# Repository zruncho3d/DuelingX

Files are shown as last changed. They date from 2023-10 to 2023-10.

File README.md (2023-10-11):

# Dueling X

**Dueling X (DX) is a flexible Fusion 360 CAD file to enable your own Dual Gantry (DG) 3D printer.**

**Dual Gantry** printers are _badass dual-head speed demons_.  

They have all the benefits of two toolheads, without the speed disadvantages inherent in IDEX printers, or the complexity and risk inherent in toolchangers.   [Here's one (Dueling Zero v3)](https://github.com/zruncho3d/DuelingZero):

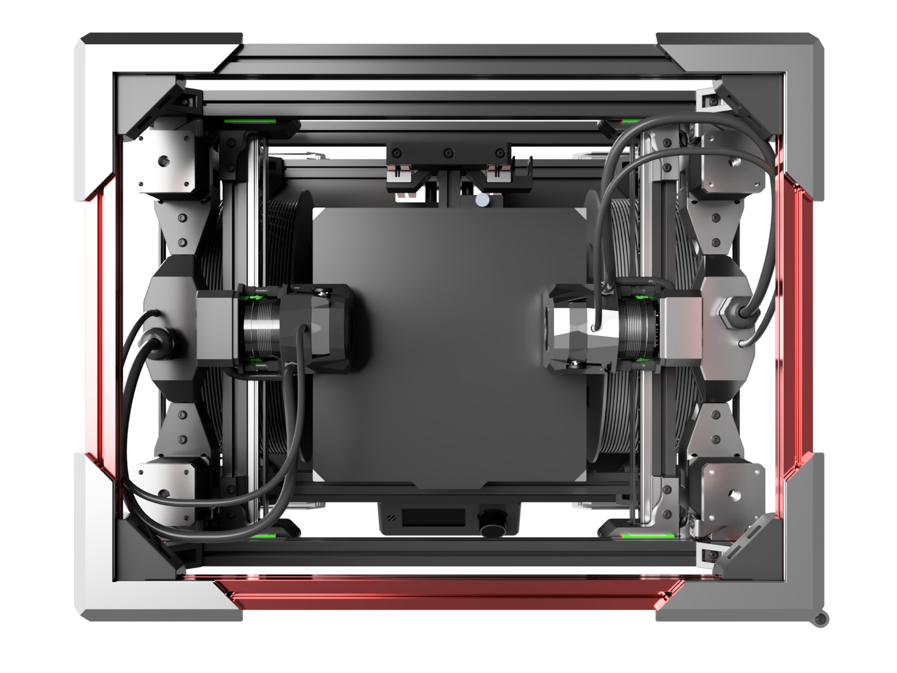
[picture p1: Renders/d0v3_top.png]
text


Not your average printer, right?  In short, the mechanical side of DG is reasonably mature, but the configuration and calibration side is still developing... so, consider it scary-but-exciting territory, for the adventurous.

**Dueling X** is a parametric gantry design based on the original Dueling Zero v3 symmetric gantry, built to enable larger and more varied DG printers.  Use the larger extrusions, rails, motors, from a Voron Trident kit, or customize the build for whatever you have on hand.

This is *not* a complete printer generator, yet.  Think of it as a printed-part generator for a gantry, with stock sizes ready to go, but which still enables customizations.  From above, the printed parts and belts paths look like this, to scale:

| Type 0 (V0 parts): Medium | Type 1 (Trident parts): Large | Type 2 (Trident Maximus parts): XL | Your own parts! |
| - | - | - | - |
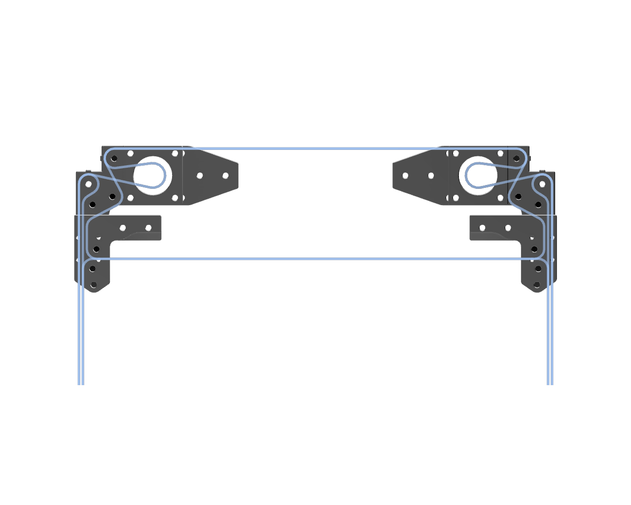
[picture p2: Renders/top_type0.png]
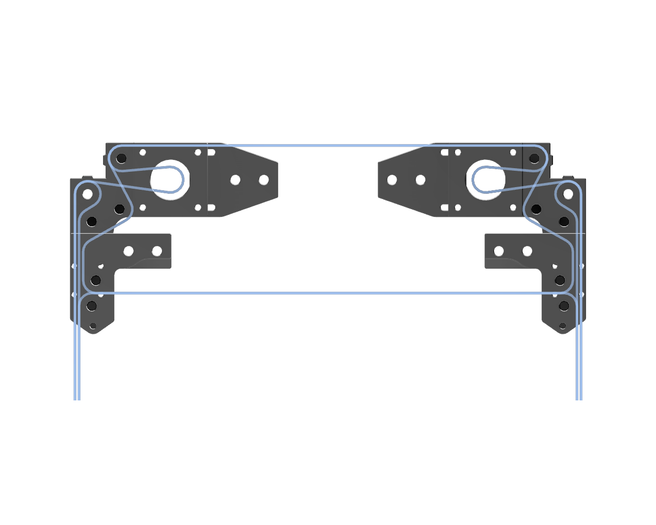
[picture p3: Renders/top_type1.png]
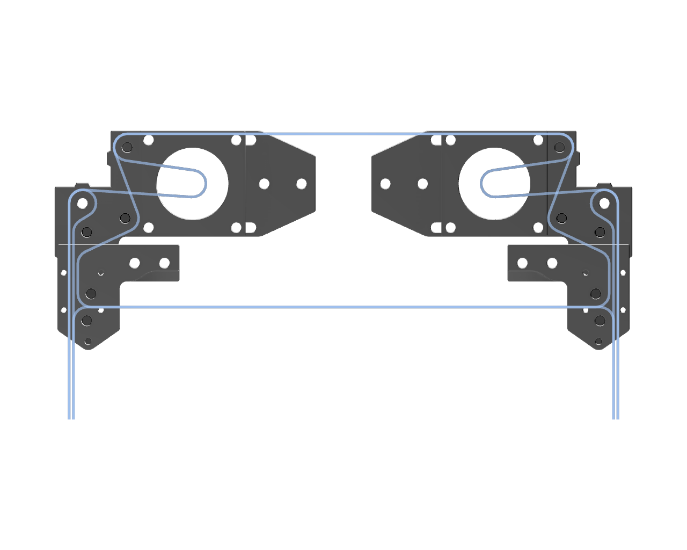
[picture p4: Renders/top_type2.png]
|  |  |  | **?...** |
| 1515/NEMA14/F623/6mm/MGN7+9 | 2020/NEMA17/F695/6mm/MGN9+12 | 3030+2020/F695/9mm/MGN12 | **?...** |

Similar shapes, yet completely different "parts bins" and sizes!

| Sample iso view | 3 stock sizes on one plate |
| - | - |
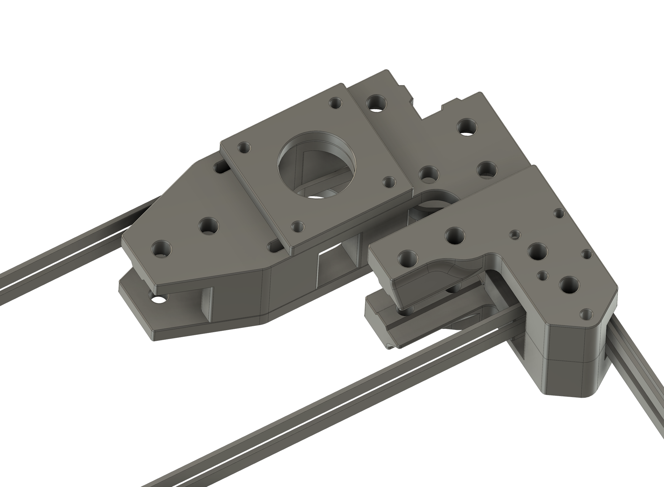
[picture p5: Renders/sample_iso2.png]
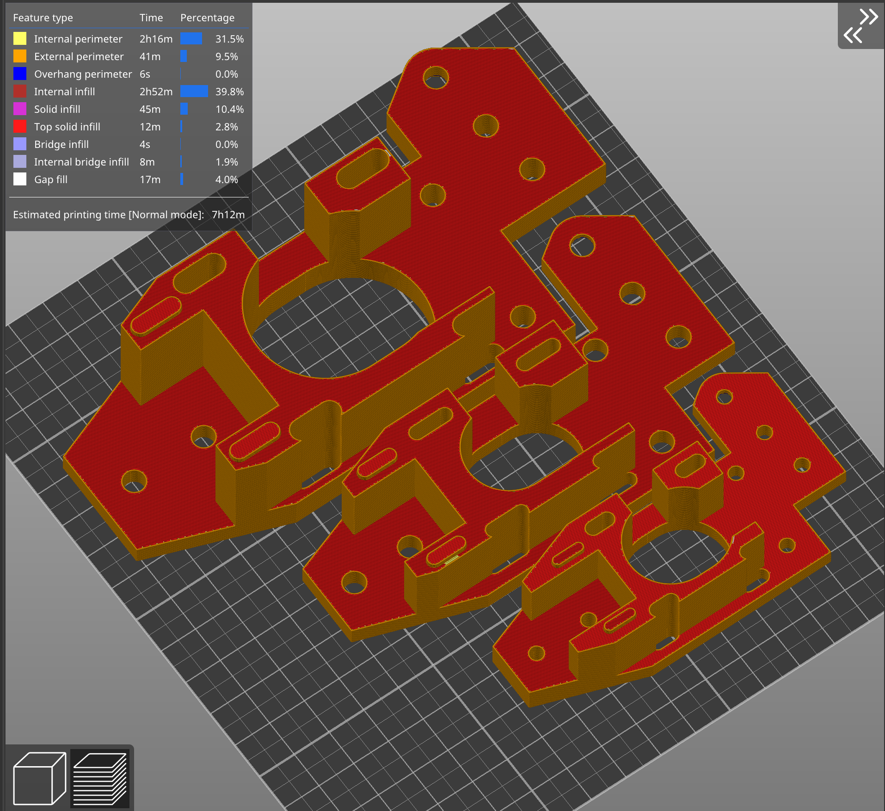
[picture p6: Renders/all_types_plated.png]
|  |  |

The STLs above were generated by changing the `type` value between the 3 values, waiting a few seconds for the model to recompute, and exporting an STL after each change.

Main features of DX:
* **3 main stock sizes (medium, large, XL)**, where each uses a different parts kit (Voron Zero, Voron Trident, Trident Maximus), but can still be customized to your preferred parts.  See the Standard Configurations table below.
* **Pandora-derived gantry**, for the win.  Top-mount outer rails, with bearings above, yields high XY density (build area relative to frame area).  
* **Front-facing toolhead rail** enables:
  * compatibility with many carriages, including small ones (Micron, Boop,...) and large ones (Clockwork, Archetype Core, ...)  
  * compatibility with many toolheads, including small ones (Dragon Burner, MiniSB, ...) and large ones (Stealthburner, Xol, Archteype, ...)
* **Symmetric design**: like the Dueling Zero v3 gantry from which it derives, Dueling X is symmetric, which heavily reduces the custom-plastic-parts count and complexity.  The P shape of the belts in a CoreXY printer are carefully nested in the XY plane, which has all kinds of benefits relative to prior approaches, at only the cost of about 10mm travel.

What makes this model possible?  Heavy use of parameters and equations in the Fusion 360 CAD.  See [this walkthrough video](https://www.youtube.com/watch?v=n0W37SkbVsI) for an explanation of how conditional parameters and naming conventions work in this file.  In the future, as Fusion 360 Configurations become available, managing the configurations may become even easier!

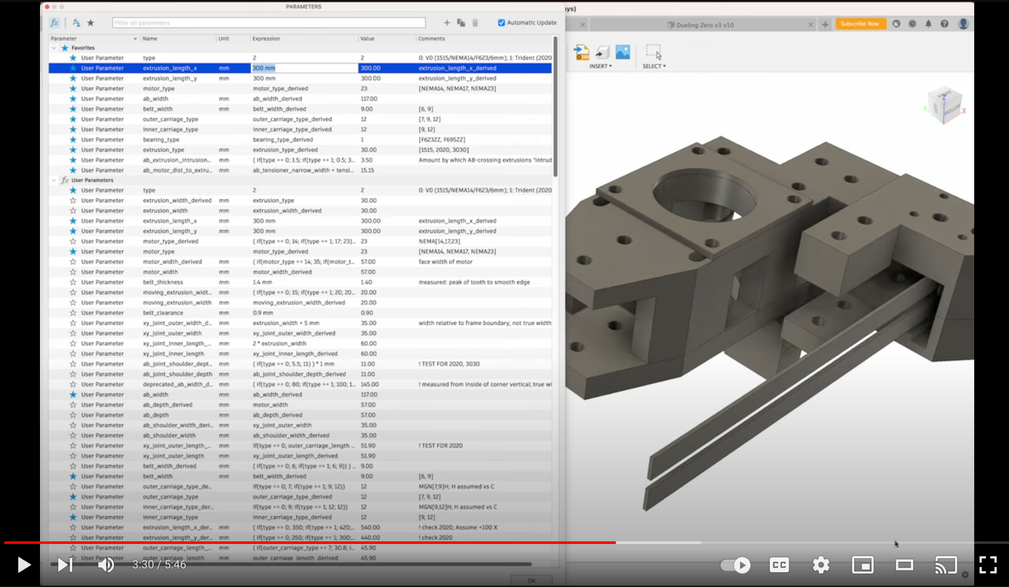
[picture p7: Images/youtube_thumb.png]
(https://www.youtube.com/watch?v=n0W37SkbVsI)


Take a look around... DG printers are weird and wonderful, yet suprisingly practical, and I'm hoping to see more builds, now that the 2020 options are available.

Like what you see?  [Buy me a coffee](https://ko-fi.com/zruncho3d) to show the love and enable future mods and content, stuff like [F0](https://github.com/zruncho3d/f-zero), [T0](https://github.com/zruncho3d/tri-zero), [B0](https://github.com/zruncho3d/boxzero), [X0](https://github.com/zruncho3d/double-dragon), [D0](https://github.com/zruncho3d/DuelingZero), [ZeroPanels](https://github.com/zruncho3d/ZeroPanels), [NoDropNuts](https://github.com/zruncho3d/f-zero/tree/main/STLs/NoDropNuts), [Boop](https://github.com/PrintersForAnts/Boop) improvements, and more.

:heart: *-Zruncho*

### What's Here?

Tons of content: a CAD file, plus documentation to make the most of it.

- #### [Stock Sizes](#standard-configurations): Choose your favorite stock size!
- #### [Custom Builds](CUSTOM.md): Customize to fit your choice of parts!
- #### [FAQ](FAQ.md): Common questions
- #### [BOM](BOM.md): Parts for stock sizes
- #### [Bugs](BUGS.md): Known issues and areas that may change
- #### [Changelog](CHANGELOG.md), [Credits](#credits) and [Support](#support)

### Standard Configurations

Each release is tested for 3 standard configurations.  Each of these three configurations (in the CAD, set by the `type` parameter to 0, 1, or 2) draws from a common “parts bin”.

<table>
  <tr>
   <td>Type
   </td>
   <td>“Parts Bin”
   </td>
   <td>Extrusions
   </td>
   <td>Bearings
   </td>
   <td>Motors
   </td>
   <td>Outer Rails
   </td>
   <td>Inner Rails
   </td>
   <td>Belt Width
   </td>
   <td>Belt Gap
   </td>
  </tr>
  <tr>
   <td>0
<p>
(default)
   </td>
   <td>V0
   </td>
   <td>1515
   </td>
   <td>F623
   </td>
   <td>NEMA14
   </td>
   <td>MGN7H
   </td>
   <td>MGN9H
   </td>
   <td>6mm
   </td>
   <td>3mm
   </td>
  </tr>
  <tr>
   <td>1
   </td>
   <td>Trident
   </td>
   <td>2020
   </td>
   <td>F695
   </td>
   <td>NEMA17
   </td>
   <td>MGN9H
   </td>
   <td>MGN12H
   </td>
   <td>6mm
   </td>
   <td>4mm
   </td>
  </tr>
  <tr>
   <td>2
   </td>
   <td>Trident Maximus
   </td>
   <td>3030+<br>2020
   </td>
   <td>F695
   </td>
   <td>NEMA23
   </td>
   <td>MGN12H
   </td>
   <td>MGN12H
   </td>
   <td>9mm
   </td>
   <td>4mm
   </td>
  </tr>
  <tr>
   <td>3
   </td>
   <td>Trident
   </td>
   <td>2020
   </td>
   <td>F695
   </td>
   <td>NEMA17
   </td>
   <td>MGN9H
   </td>
   <td>MGN9H
   </td>
   <td>6mm
   </td>
   <td>4mm
   </td>
  </tr>
  <tr>
   <td>Custom
   </td>
   <td colspan="8" >Whatever you have… any of the choices above, via parameter overrides.
   </td>
  </tr>

</table>

Overrideable parameters, mostly for subtypes, look like this:

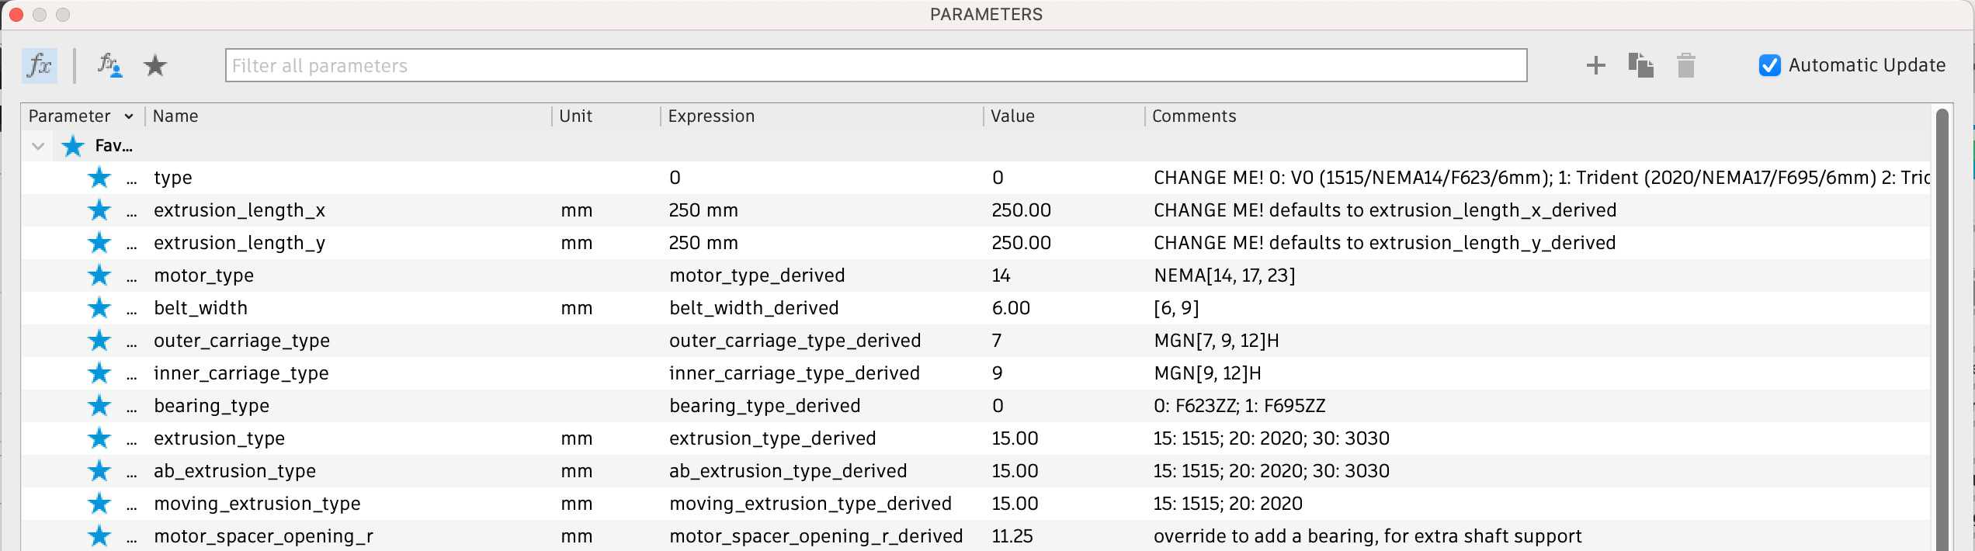
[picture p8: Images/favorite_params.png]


Lots of dimensions are then set automatically, based on these configured subtypes.  For example, the bearing type drives the bearing's flange width, ID, OD, and height dimensions, as well as the corresponding washer thickness:

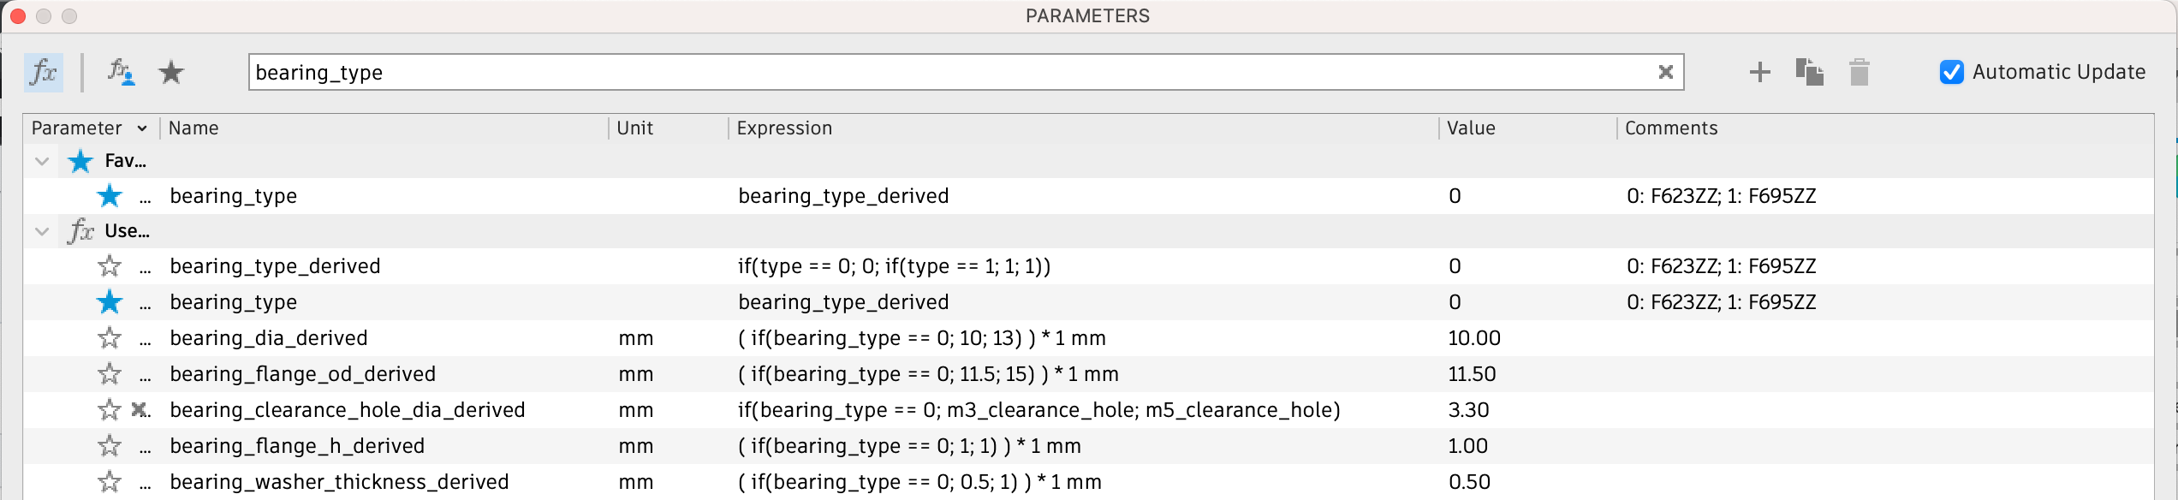
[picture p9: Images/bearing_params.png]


### Properly Parametric Design... it's hard

In a “properly parametric” design, every parameter based on an underlying configuration type (think: medium, large, XL) has a type-dependent value.

Here's an example of setting rail sizes, based on the main `type` value (see the `_derived` expressions):

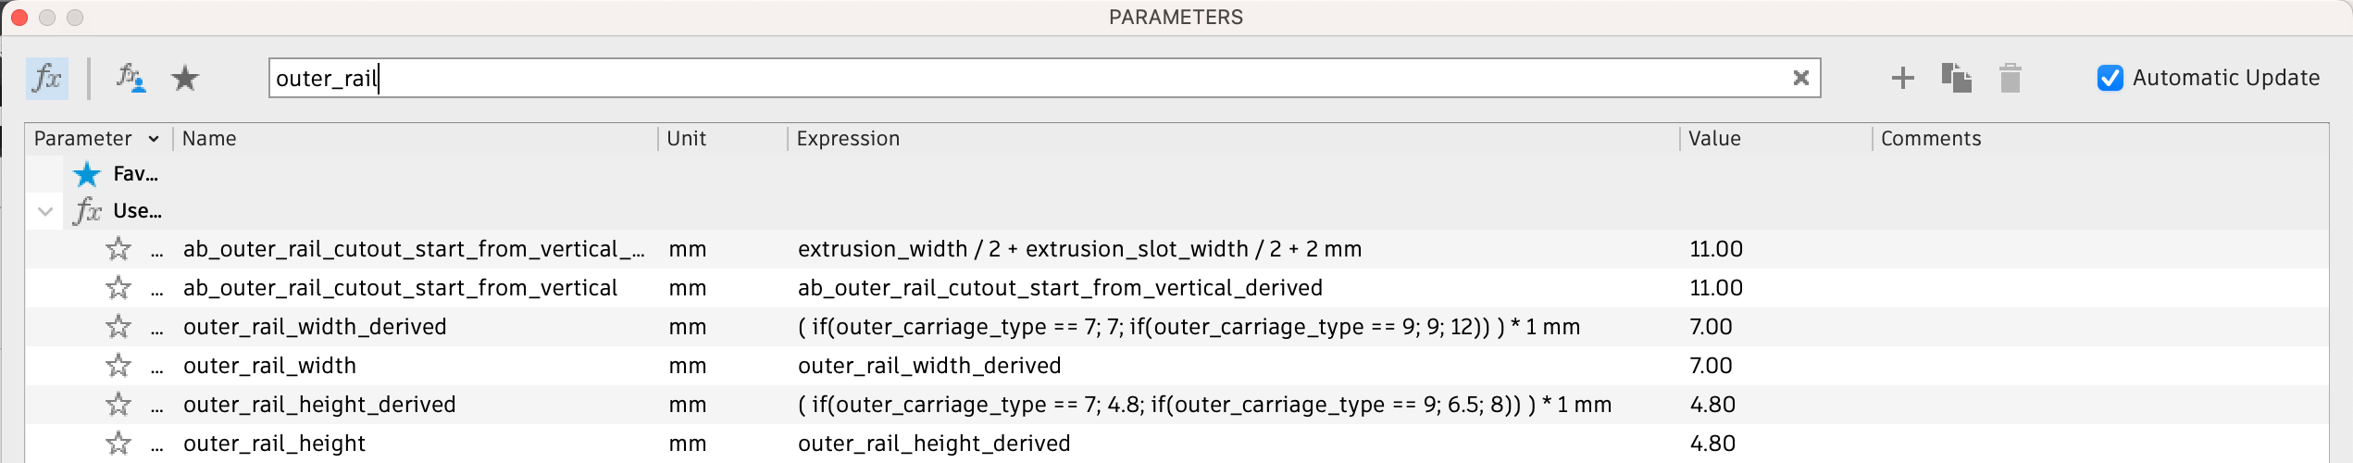
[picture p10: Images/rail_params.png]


This approach is a pain to get right, but it drastically reduces your effort to make a customized gantry design, and it makes things maintainable for the creator.  After setting the `type`, you can go straight to exporting STLs, though you’ll probably want to do a few more things:
* design X and Y endstops
* add bearings, a carriage, and toolheads to the generate CAD
* tweak a few parameters, if customizing anything
... but all of that is straightforward and explained within this repo.

You'll also need a printer frame around it, of course.

Beyond "just" being properly parametric, this design is scalable, where many parameters are set using an equation, rather than being hard-coded based on a few types.  However, if a parameter isn't working for you - that is, it causes a misalignment with your parts, or just doesn't look right - all key parameters are overrideable anyway, as the CAD uses a convention where each parameter is set by default to a corresponding `_derived` value.  You can always change this value, and you'll know exactly what to set the model back to later if you want to restore the default (the same name, plus `_derived`).  Poke around in the parameters list and you'll see many `_derived` values.

## What’s the status?

**Alpha.**  It’s a soft launch.  There’s one place to see changes and CAD files, with all dev in the open… but any future release may change parts and designs in a way that invalidates _everything you just printed_.  Alpha here means _anything may change_.

**However,** the quality standard is unusually high: for any update, all standard types will have documented checks - both visual and measured - to ensure that they could work in practice.  The 1515-based config (Type 0) is based on dimensions aligned with Dueling Zero files, which have been printed and built, and are known to be good.  For the Type 1 and Type 2 sizes, no builds have proven out all the dimensions, yet.

If you’re building this, or any dual gantry printer, **you’re an alpha tester** - which means you are responsible for confirming all dimensions beforehand in CAD, as well as being confortable with the expectation that you’ll have to do a reprint or two.   

## Getting Started

A few notes, before you begin, for success:
* The amount of tensioner travel is 8mm for Type 1 and Type 2.
* Formed threads are used heavily for the other side of bearings.  When assembling, don’t gorilla these.  Smoothly add torque and stop when you see the gap close to zero.
* Check that any parameter marked `MEASURED` matches measurements for your setup: mostly, belt thickness.

ALWAYS print the test part, corresponding to your desired type, first.  This part will ensure that values which vary with printer, or vary with parts vendor, are set to match your setup, before wasting filament.  After printing:
* Add an extrusion and match the slots to them.  Needing to use the edge of the extrusion to scrape the tab is a good thing.
* Put an extrusion in to the slot, along with nuts or t-nuts, to ensure that screws can screw in without bottoming out.  Lock the screws down.
* Put a bearing-size screw into the formed thread hole.  Make sure you can start it easily.  Stop when you feel a bit of resistance.
* Ensure that the screws for your bearing size have sufficient clearance in the sample counterbore.

If you have issues, look in the parameters list for `NEEDS TEST` and modify the ones for your size(s).

With params set, export 10 STLs: upper/lower x top/bottom XY joints, upper/lower x AB blocks, motor spacer, tensioner.  Reorient; should be obvious how (side with the 0.4mm chamfer to the bed).

**Print settings:** standard Voron settings; higher infill on the XYs can’t hurt.

**DO NOT** print all copies of a part before assembly.  Print out and test one part at a time ideally, and definitely not more than one corner assembly, without validating that it works.

### Credits

All this descends from the Dueling Zero project... seriously, [go there](https://github.com/zruncho3d/DuelingZero) if you haven't yet, as it has all kinds of software and firmware info.  Beyond that:
* Heavy credit goes to `Desune` for the parallel design for [Dueling Boops](https://github.com/desune2487/Dueling_Boops), which influenced many choices.
* The gantry design was heavily influenced by the Pandora / [Pandora's Box](https://github.com/MasturMynd/Pandoras_Box) gantry (`MasturMynd`); the [Trident Maximus](https://github.com/MasturMynd/Trident-Maximus) build was selected by community vote to the Type 2.
* Future CAD will use parts from [the Construct](https://github.com/PrintersForAnts/Voron-Construct/tree/main) (`kyleisah`), as well as the [Micron](https://github.com/printersForAnts/micron) CAD (`hartk`).

### Community

There's a `#dueling-zero-dev` thread within the `#tri-zero` channel, and now a `Dueling X` user project, on the [DoomCube Discord](https://discord.gg/doomcube).  Put your question on the channel, so the community can answer first, please; no DMs.

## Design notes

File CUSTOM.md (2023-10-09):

# Custom configurations

Say, you want to make a variant, like 1515 + NEMA17… will it work?  You may need to tweak some positions to ensure clearances.  Ensure the conditions below to make sure your Dueling X build can actually be assembled, uses screw sizes that exist, and can actually move.

Think of it as a giant puzzle that you have to solve.

Or… **get** to solve.  I prefer the (more thankful) latter interpretation.

First, set the type value to the closest one to your target, to minimize the number of parameters to override.

To see a model in a non-default type, open the f3z, go to the parameters screen, and change the type value from the number 0 to 1 or 2.  Assuming your Fusion install is set to recompute parameters automatically (the default) the model will then adjust to the new size.

## What can I customize?

All of the stuff that has a corresponding `_derived` expression is meant to be customized; the `_derived` expression is effectively a default, for the `type`.

To set a value, go to Parameters and give it a value you want, vs the `_derived` version.

Sample parameters that you may want to override (customize):

* Extrusion widths: main (outer rails) + moving + "AB connector"; each can be different!
* Width (X dimension)
* Length (Y dimension)
* Belt width
* Rail/Carriage sizes
* Bearing sizes: example - 2020 with F623 bearings for more travel
* Motor type/size
* Plate thicknesses (against the motor, and on top of the ABs)
* Center diameter of motor spacer (to enable double-supported motors, by adding another bearing on the end)

This list is not exhaustive; there are also other parameters that decide where the bearings go, from which all other part shapes are derived.  For example:
* `xy_joint_carriage_offset_from_moving_extrusion_rear` moves the carriage position up or down on the model.

## Examples of customizations

### Double-supported motors

Easy!  Change `motor_spacer_opening_r` to a new value.

### Wider outer carriages

Say, not so hypothetically, `shadow_steve` seeks wider outer carriages (the rails with two carriages).  

Steps: replace the default `_derived` value: set `inner_carriage_type` → 9
Then follow steps below to see what stuff to check and what params to adjust At least these two are needed:
* `ab_joint_shoulder_depth` → 12mm
* `xy_joint_carriage_offset_from_moving_extrusion` → 3.4mm
If all the items below are OK, plus a full section analysis check out, you can move to STLs!

# How do I navigate the model?

Start with the base sketch!  Everything derives from this, like the belt paths, bearing positions, XY joint positions, and resulting travel.  Every single dimension here is critical.

Anything which is not strictly dependent on the bearing and extrusion positions gets its own sketch, which should use an absolute minimum of references to base sketch geometry, to minimize model fragility.  So often, you'll need to find the right sketch after the base one to understand a parameter and change it.  All sketches are labeled, to make this search process a little faster.

Use the timeline as much as you can to navigate the model effectively.  If you're just changing the ABs, go there first, and then switch between types with less recomputation delay.  Stepping through each group of features makes it much faster to find what you want.

# Pre-printing Checks

More details to be added here... this section notes checks to do before generating STLs (whether you for your custom build, or Zruncho at release time)

You want to ensure 3 things:
* Prints can succeed
* Printed parts are sized to match real parts
* Gantry can actually be assembled

These sound obvious... but it's possible to get them all wrong.

### Condition: Belt path is possible

A belt can't pass through a bearing.  You may have to tweak some values so that this is the case!

### Condition: Generally good parts for printing

No overly thin walls, no unsupported overhangs... typically a section analysis through the whole model will reveal these.  

Sometimes area selections get silently lost when parameters change, and the only way to catch those is to scan the whole model visually.

### Condition: Access to tighten outer carriage screws

… or at least with an amount of tilt so small that you can still get the driver in.

Param to adjust: `xy_joint_carriage_offset_from_moving_extrusion`

Potential values in `xy_joint_carriage_offset_from_moving_extrusion_derived`

Process: adjust the timeline position to after the XY joints are created.  Click on the belts to highlight them in blue.  Look for a gap through which an allen driver can be inserted, without impacting the bearing flange.  Look at the `Carriage Alignment` sketch, which decides the positioning of carriage bits.

With Type 0, there’s no way around a tight fit; MGN7H carriages have a long-carriage-direction screw spacing that nearly matches the flange OD of F623 bearings.  So one of the carriage-screw holes must be aligned between the two moving bearings, and then you hope that the bearing on the other side has clearance.  The location is manually aligned by moving the carriage holes relative to the bearings on XY joints.  

### Condition: Sufficiently thick walls at rear edge of XY

Param to adjust: `ab_joint_shoulder_depth`

Solutions can include increasing this value to enable a complete counterbore for the rearmost XY-joint carriage screw OR reducing it to have a partially-overlapped hole (like the 1515 version).

### Condition: Sufficient belt clearance between frontmost two outer AB bearing stacks

Param to adjust: `ab_exposed_bearing_y_spacing`

Param to adjust: `ab_innermost_bearing_rear_y_offset_derived`

The smaller this is, the greater the potential moving-extrusion travel.

### Condition: viable screw lengths exist to match all holes

Especially if changing AB part thicknesses (say, due to modifying belt widths), you have to ensure that all screws have enough length to fully form threads.  

**Screws for bearings**: check them all; these are the easier ones.  You need a few mm of screw engagement in the formed threads.

**Front AB bearings**: adjust `ab_front_bearing_counterbore_dia` so front screw head is contained, yet, screw does not stick out, and also has a little travel to fully compress the counterbore there.  M5 example: 9.5mm dia, 2.75mm head thickness.

**Motor screws**: The motor spacer part provides a lower-plastic way to get the height right for motor screw, without needing to adjust everything else to be thicker.

# Release Process

For releasing the whole model, the checks are broader that those of a single variant.

### Condition: Parameters can be varied (DX releases only)

Mostly: change the type in both directions (0 - 1 - 2 - 1 - 0) and ensure no yellow warnings or red errors appear in the timeline.

Then vary all the favorited parameters and ensure that huge values don't create issues either.

Both of these can break without you noticing, and sometimes parameters can compute nondeterministically, where it appears to randomly break.  When this happens, you may need to change the kinds of constraints that are used in base sketches or break complex features into multiple stages or sketches.  It feels like a dark art, until you internalize what's really going wrong.

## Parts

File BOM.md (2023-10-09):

# Bill of Materials

Multiply by 4 for a double-side full Dueling Gantry and add screws as desired for the rails.

## Type 0: V0 parts bin

Per XY joint:
* 3 m3x35 BHCS
* 4 m2x6 BHCS/SHCS
* 2 m3x16
* 2 m3x12
* 4 m3 nuts
* 4 F623 bearings
* 4 precision m3x0.5 shims

Per AB block:
* 1 m3x25 BHCS (front)
* 3 m3x30 BHCS (most bearings)
* 1 m3x45 BHCS (rear side bearing through-hole if no corner used; otherwise (likely) m3x50)
* 4 m3x35 BHCS (motors)
* * 1 m3x25 BHCS (tensioner)
* 2 m3x10 BHCS (bottom extrusion)
* 2 m3x12 BHCS (top extrusion)
* 1 m3x6 BHCS (side extrusion screw)
* 6 m3 nuts (extrusion, side screw, long screw)
* 1 m3 heatset
* 14 F623 bearings
* 14 precision m3x0.5 shims
* 3 plastic spacers (get from Pandora repo; should be thin)

## Type 1: Trident/V2 parts bin

Per XY joint:
* 1 m3x40 BHCS (front)
* 2 m5x40 BHCS (bearings)
* 4 m3x6 BHCS/SHCS
* 4 m5x16 (extrusion screws)
* 4 m5 t-nuts
* 4 F695 bearings
* 4 precision m5x1 shims

Per AB block:
* 1 m5x30 BHCS (front)
* 3 m5x35 BHCS (most bearings)
* 1 m5x50 BHCS (rear side bearing through-hole if no corner used)
* 4 m3x40 BHCS (motors)
* 1 m3x30 BHCS (tensioner)
* 4 m5x10 BHCS (inner extrusion screws)
* 1 m5x6 BHCS (side extrusion screw)
* 6 m5 t-nuts (extrusion, side screw, long screw)
* 1 m3 heatset
* 14 F695 bearings
* 14 precision m5x1 shims
* 3 plastic m5x10 spacers (no part made available)

## Type 2: Trident Maximus parts bin

TBD

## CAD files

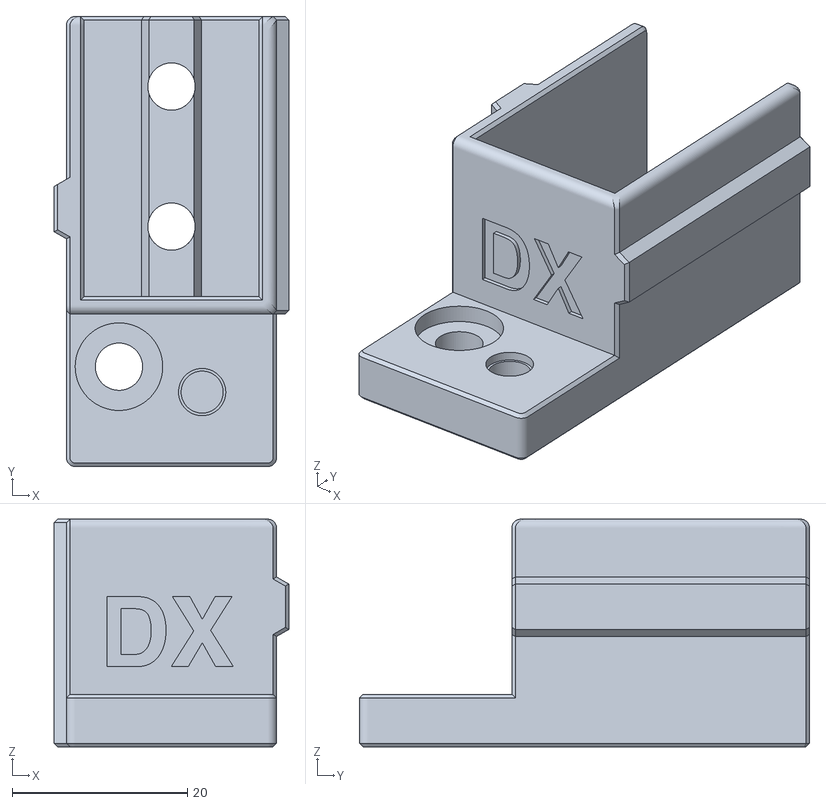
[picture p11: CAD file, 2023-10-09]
STLs/TestPiece_Type1.stl
26.8 x 51.4 x 26.0

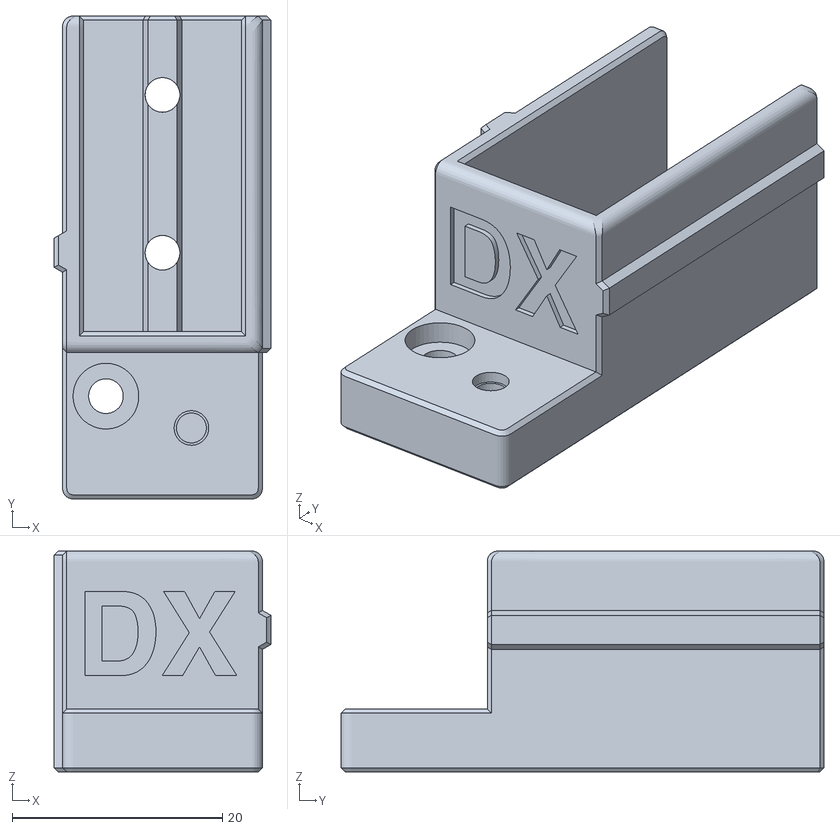
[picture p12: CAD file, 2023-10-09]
STLs/TestPiece_Type0.stl
20.6 x 45.9 x 21.0

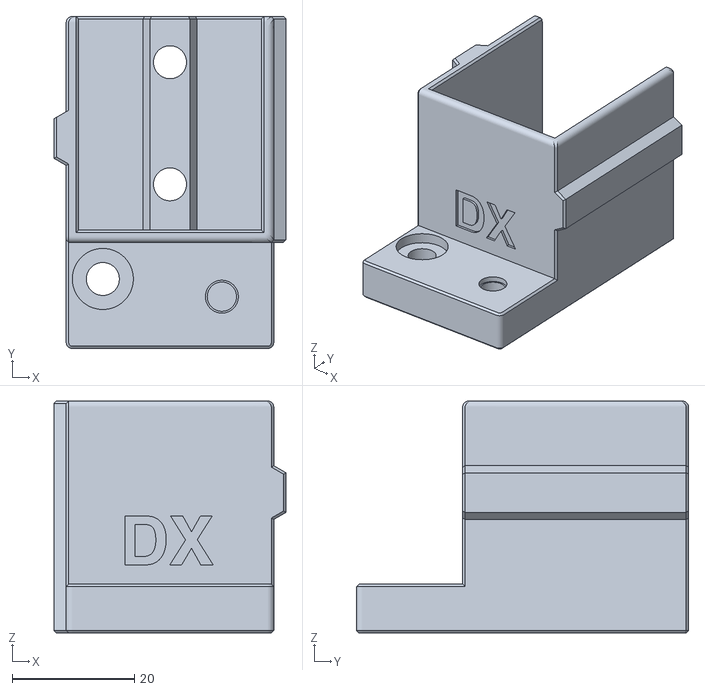
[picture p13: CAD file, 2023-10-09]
STLs/TestPiece_Type2.stl
38.0 x 54.4 x 38.0

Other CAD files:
CAD/Dueling_X_Gantry_v80.f3d

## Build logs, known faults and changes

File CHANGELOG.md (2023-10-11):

### Changelog / Updates

* 2023-10-11: v80
    * Add Type3, which is Type1 + MGN9 Inner, per request.  This is a pretty reasonable choice to use Boop or Micron carriages on a larger printer; saves weight.
      * ab_joint_elbow_fillet_r_derived: min(ab_motor_dist_to_extrusion + extrusion_width - xy_joint_outer_width - const_fillet_r_medium; ab_joint_shoulder_depth - const_fillet_r_medium)
      * ab_joint_elbow_fillet_r = ab_joint_elbow_fillet_r_derived
      * In ‘AB inner elbow fillet’ feature, change to use fillet_r
      * inner_carriage_type → 9
      * ab_joint_shoulder_depth → 12mm
      * xy_joint_carriage_offset_from_moving_extrusion → 3.4mm
    * Add moving_extrusion_overlap, which adds an override to extend the XY joints farther inward, and adjusted sketches to use it
    * Minor doc and attribution fixes
* 2023-10-09; v76
    * Finish test piece to ensure unknown values are reasonable.  Has extrusion tab slots in 3 orientation, holes that match the ab extrusion spacing, clearance holes, formed thread holes, and bearing screw clearance holes.
    * Fix under-constraint error for X location of AB lower/upper locking tabs
    * Add instructions for testing the test part
    * Finish all documentation and edit for clarity and conciseness (I know, I know…)
    * Document relationship between Dueling Zero and Dueling X
    * Push to GitHub as private and wait to flip the bit to make this thing public!!!
* 2023-10-08; v74
    * Type 2: Tweak params to get 10mm-aligned AB extrusion length (ab_extrusion_width_computed)
    * Add motor_spacer_opening_r to easily enable the motor plate to fit a bearing
    * Clear away all obsolete and unused parameters
    * Tag all parameters that require tuning
    * Definite minimal set of favorite params
    * Make progress on test part to ensure correct values for tunable params
* 2023-10-07 v71
    * Fix model break when either extrusion_length_x parameter is changed, or when type is cycled
      * Remove all top-edge fillets, to simplify debug
      * Remove an inadvertently split line in the base sketch, then fix all broken downstream references
      * Fix a computation failure by switching to a parallel constraint instead of a tangent one
      * … and it seems more stable now
    * Docs mostly converted to Markdown for Github usage, with exception of pre-release checks (which are getting defined)
* 2023-10-02 v70
    * Fix thin-wall error near Type 1 tensioner heatset hole
    * Add back extrusion hole to the side
    * Label all sketches, work planes, features, groups, and bodies appropriately
    * Components for everything
    * Ensure easy-starts with hole chamfers
    * Ensure feasible screw sizes: adjust XY joint top height, XY joint lower thickness, and AB bearing hole depths
    * Create BOM for Type0 and Type1 XYs and ABs
* 2023-10-01 v62
    * Generalize AB-connector extrusion from main frame extrusion (narrower if you want); update lots of dimensions to match
    * Add inner corner fillet at the AB elbow
    * Add extrusion slot tabs to ABs
    * Fillet and chamfer ABs
    * Add top-edge chamfers
    * Angle leading edges of extrusion slot tabs
    * Add mirrored side of XYs, with flipped filling
    * Fillet XY elbows
    * Smoothen wire-clearance cutaways on XYs
    * Add extrusion slot tabs to XYs
    * Fillet and chamfer XYs
    * Mirror ABs and belts and join belt bodies
* 2023-09-30: v52
    * Fix thin-wall error in AB lower tab
    * Fix rear tensioner heatset location; was too far back
    * Tweaked key params for Type 1 and Type 2 setups for carriage-screw access and to fix belt-bearing interferences: `ab_exposed_bearing_y_spacing, ab_innermost_bearing_rear_y_offset_derived`
    * Fix belt interference with ABs
    * Fix unmatched AB extrusion tip
    * Fix front AB clearance
    * Fix scaling of rail cutout in AB near rear bearing hole
    * Fix XY and AB heights so that all outer carriage screws can be inserted in-place
    * Fix XY top thickness to scale
    * Close rear bearing hole on Type 2
    * Make XY allen clearance holes parametric and larger with Type 1 & 2
    * Improve X travel to max possible for Type 1 and Type 2
    * Add cutouts for carriage clearance, scaled to type
    * Add bridged counterbore for front AB bearing screws to clear + adjust for each type
    * Make motor spacer thickness parametric + adjust for each type to fit known screws
* 2023-09-25: v42
    * Add filling in the XY joints
    * Fix annoying-af nondeterminism that was breaking the base sketch when 0-2-0 switching
    * Fix overlap on larger types with XY front hitting ABs
    * Add belts
* 2023-09-24: v35
    * Reduce cutaways by tensioners, heavily
    * Reduce plate overlap with extrusions and make parametric
    * Using measurements taken from Trident, reduce width with denser screws: 9mm to edge, 16mm between, vs 10/20mm previously. Now the 2020 version fits on a V0 plate (117mm wide)
    * Fix thin wall in rear, near motor screw
    * Expand tensioner ramp and made it parametric: ab_tensioner_front_ramp_min_thickness
    * Add belt travel; now 8mm for 2020; less than Trident’s 10mm at the moment, but better.
    * Tensioner heatset setback matches screw travel now
    * Temporarily remove side extrusion screw holes; will likely be replaced with two screws in the future, but larger changes
    * Define critical param to align carriage: xy_joint_carriage_offset_from_moving_extrusion_derived
    * Create XY upper and lower bases, then validate for 3 sizes; still needs the middle bits added, plus cutouts for endstop clearance
* 2023-09-23: at v21
    * Define and use belt_rear_clearance to pull bearings near verticals and reduce overall width
    * Define width of ABs based on geometry
    * Added tensioner ramp and matching tensioner; redid all related geometry to ensure bearing clearance and sufficient space forl tensioner travel.
    * Added side extrusion-grab hole
    * Rename motor_slot_length → tensioner_travel
* 2023-09-22: v15
    * Make frame extrusion type an explicit param
    * Add type 2 and corresponding values: Trident Maximum Duelingus: 3030+2020, NEMA23, F695, all MGN12
    * Added constraints to make type 2 look right
    * Scale width of motor pulley access hole with extrusion size
    * Marked all most-likely-to-change parameters as favorites
* 2023-09-XX: Time to rebuild from scratch
    * Rebuilding is painful, but sometimes it’s the only way to make progress.  The D0 v3 CAD was freshly recreated from the v1 CAD, but with compute failures in the base sketch, it’s really hard to debug what parameters are colliding, as well as even navigate within the model.  If you want to have multiple sizes in a model, you can slowly refactor it there, or you can start from the beginning, leveraging what you know, and testing continually to make sure all sizes don’t have issues.
    * Decision taken to start over, and leverage conditional parameters from the beginning, as well as multiple, more hierarchical sketches.  This means:
        * Define at least two configurations before building the model - “types” - V0 + Trident sizes
        * Define many parameter values (_derived) ones based on the type, using if statements in the parameters dialog
        * Aggressively test all new features against all types to ensure that things are scaling
        * Generalize parameters wherever possible
* 2023-09-16:
    * Dueling Zero stream on DoomCube live goes well!  Peaks around 80 viewers.  
    * Interest seems more for 2020 than 1515, which makes a lot of sense. Larger builds are more practical and kits have dropped the prices for Tridents and V2s lately.
    * Time to make this happen, finally.  At this time, Dueling X is really more an idea than an implementation; the D0 v3 CAD has lots of parameters, but alternate sizes were not tested.

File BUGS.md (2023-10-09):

This is a list of known issues and possible improvements for the future.

Bugs:
* Thin wall at rear of lower XY with Type 2

Improvements:
* Generally, enable a stronger gantry when freestanding
* Add hole on the side of the ABs to connect to the vertical extrusions
* Add option for heatsets or nuts, vs larger-size formed threads
* Slightly improve elbow thickness of XYs and suitability for plates by changing the Y positioning of the `ab_exposed_bearing_y_spacing` to be somewhat higher.
* Reposition rear extrusion to enable a large contiguous space for cables, bowden, or more?
* Consider vertical motion for tensioners

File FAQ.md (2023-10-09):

# FAQ

## What is a Dual Gantry printer?

Dual Gantry is a printer layout that enables all the capabilities of a second toolhead (multi-color, multi-material, soluble supports, multi-part), without the complexity and risk of a toolchanger’s attachment interface, or the speed drawbacks of an IDEX.  But in engineering there are always tradeoffs, and the downside is some additional cost, build time, and unknown calibration complexities.

See [Dueling Zero](https://github.com/zruncho3d/DuelingZero) docs for more explanation, including the software side (which is really interesting if you want to have all of the XY space availalable for each extruder's use).

## What's the catch?

A few things...

For some sizes, the carriages stick outside of the frame boundary defined by the extrusions slightly, requiring a panel gap to be covered by something like ZeroPanels (for 1515) or foam tape.  That's not the case for all other Voron gantries, which fit inside the frame.

The specific design doesn't have much attaching to the outer-rail extrusions, so it's not as strong by itself as other designs.  Once in the frame, and braced there with blind screws, it should be fine, though.

The level testing isn't high, either.

And oh yeah, the calibration side can best be described with a question mark.

## Why doesn't this project use the Configurations feature in Fusion 360?

As of October 2023, Configurations is still rolling out slowly to Fusion 360 users.  Since it isn't available to everyone yet, it isn't the default.  

Configurations is made for exactly use cases like this one, though!  Instead of a massively long list of parameters, lacking any organization, and with complex, hard-to-read, hard-to-change nested conditional expressions, Configurations would bring order to the chaos.  And beyond the parameters, you could selectively enable things like the motor spacers on a per-configuration basis, as well as avoid the whole override setup that doubles the number of parameters.  Maybe soon?

Check the ["Configurations Lite" video](https://www.youtube.com/watch?v=n0W37SkbVsI) for more.

## How are Dueling Zero and Dueling X related?

D0 came first.  It was the first open-source, fully-documented, Dual Gantry CoreXY printer design.

DX is a generalization.  At least at the initial release, the bearing positions for DX-Type0 exactly match D0v3... that work bootstrapped this.  

Over time, DX-Type0 is likely to diverge; it has to favor simplicity and ease-of-porting-to-other sizes.

As of the initial release (Oct 2023), there's really no strong reason to go with DX-Type0 over D0v3.  The D0v3 gantry parts have been tested in at least one build, twice ('cuz they're symmetric...) so they're known good.  DX-Type0 _should_ be good, but until you build it, you don't know.

However, D0 includes a complete printer CAD, including integration with a Tri-Zero base and BoxZero frame.  So if you want to make a change (like NEMA17) but keep the 1515 extrusions, you could do that with DX-Customized-Type0 parts inside a D0 frame!

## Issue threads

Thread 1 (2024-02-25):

CAN Bus Setup for Dual Hotend 3D Printer

Nico4589, 2024-02-25:
Hello, I have come across your project, and it is quite intriguing. I am currently in the process of developing a printer with a dual hotend, and I am interested in implementing CAN bus communication for the two printing heads, as you have done. Could you kindly provide a comprehensive guide on the electrical connection of the bus cables and the configuration of communication channels? While I have reviewed your configurations for the right and left sides, I am struggling to comprehend the underlying logic of its functionality. Your assistance on this matter would be greatly appreciated. Thank you.

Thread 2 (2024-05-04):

Simpler CoreXY belt alternative

TheOnlyBeardedBeast, 2024-05-04:
Hi I am really fun of the dueling zero, and the duelingX gantry, it made me think a lot.

CoreXY really makes sense in its base configuration but for the dual gantry many additional idlers were added which is a work of art but adds additional drag to the belts, What about this belt configuration could be used with annex k3 style motors and mount (longer shafts so each shaft acts as an idler and drive shaft) and maybe it would be easier to have this belt setup parametric?

This belt setup is has still corexy kinematics, the downside is that the xy joints need to be a bit wider and they have to be T shaped like ratrig or the vzbot, but no additional idlers are needed to achieve a nice dual gantry printer.

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

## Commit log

2023-10-09 Initial release of Dueling X
    [Dueling_X_Gantry_v76.f3d, TestPiece_Type0.stl, TestPiece_Type1.stl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]
2023-10-11 Add Type3 - Type1 with smaller MGN9 inner rail
    [Dueling_X_Gantry_v76.f3d, Dueling_X_Gantry_v80.f3d]
2023-10-11 Correct note about travel
    It only increases if the motors are much larger
